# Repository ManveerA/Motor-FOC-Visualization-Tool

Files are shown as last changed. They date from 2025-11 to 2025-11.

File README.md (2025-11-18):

Repository for the project: Real-Time Hands-on Tool for Teaching Three-Phase Motor Control

Youtube Demo: https://youtu.be/jReT5BAICFI?si=BRLmQ3dqiokIST9U

Contributors:

Manveer Aujla - manveeraujla0226@gmail.com

Gavin Feher - gavin.feher@gmail.com

Adam DePinto - depintoadam@gmail.com

Last updated: 2025-11-17

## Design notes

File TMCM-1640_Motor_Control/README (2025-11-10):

The Trinamic Motion Control Language (TMCL) script for controlling the TMCM-1640 controller/driver to drive the QBL4208 BLDC motor.
Author: Manveer Aujla
Contact: manveeraujla0226@gmail.com

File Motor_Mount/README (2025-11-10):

Design files for the custom 3D-printed coupled motor mount.
Designer: Adam DePinto
Contact: depintoadam@gmail.com

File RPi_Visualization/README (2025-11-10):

All files pertaining to the visualization, including the Python script running on the Raspberry Pi and the TI LAUNCHXL-F28379D (LaunchPad) MCU firmware code.
Author: Gavin Feher
Contact: gavin.feher@gmail.com

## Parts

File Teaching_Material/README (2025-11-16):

FOC teaching materials for the proposed approach.

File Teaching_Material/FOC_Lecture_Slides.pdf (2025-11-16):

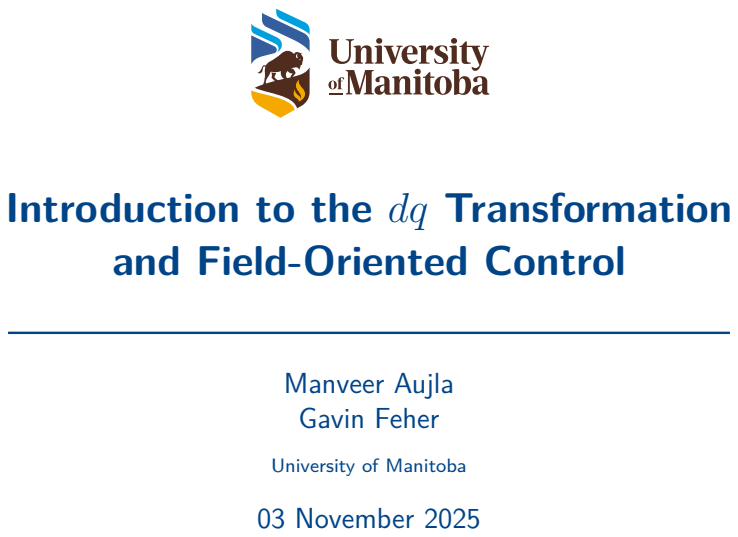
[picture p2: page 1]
Manveer Aujla Gavin Feher; 03 November 2025

Introduction to the dq Transformation
and Field-Oriented Control

University of Manitoba

## The Control Problem

In general,
- Speed control requires torque control for actuation
- Torque control is also current control from proportionality: τ = Kτ i
- Bandwidth: Torque ≫ Speed

Cascaded Control Structure:

Σ

+
PI | Σ

+
PI | Power Stage | Motor

i

∗ | ei | v | i
Speed Loop | Torque Loop

ω

∗
m | eω | ωm
− | −

## Torque Control in a DC Motor

In four steps,
1. Measure the controlled current flowing into the motor.
2. Compare measured current with the desired current, generating error.
3. Amplify the error signal using a PI to generate a correction signal.
4. Modulate the correction voltage and apply to the motor terminals.

## Three-Phase Motors

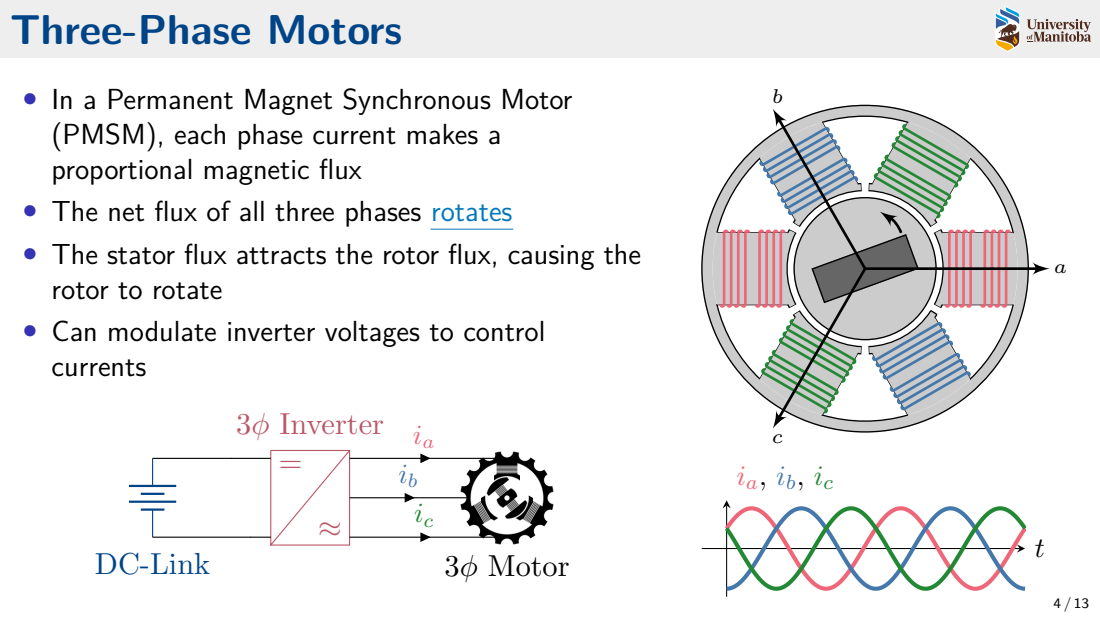
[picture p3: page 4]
DC-Link; 3ϕ Inverter; 3ϕ Motor

• In a Permanent Magnet Synchronous Motor
(PMSM), each phase current makes a
proportional magnetic flux
• The net flux of all three phases rotates (https://www.desmos.com/calculator/sqiyzcerde)
• The stator flux attracts the rotor flux, causing the
rotor to rotate
• Can modulate inverter voltages to control
currents

## The Clarke Transformation

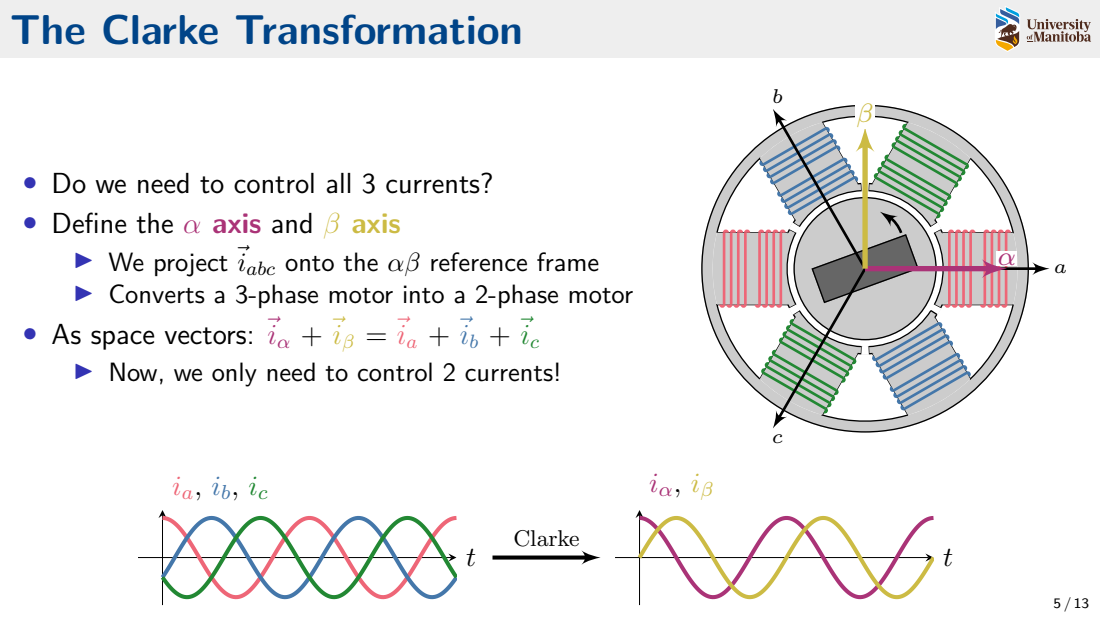
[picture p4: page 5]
Clarke

• Do we need to control all 3 currents?
• Define the α axis and β axis
▶ We project ⃗iabc onto the αβ reference frame
▶ Converts a 3-phase motor into a 2-phase motor
• As space vectors: ⃗iα + ⃗iβ = ⃗ia + ⃗ib + ⃗ic
▶ Now, we only need to control 2 currents!

## The Park Transformation

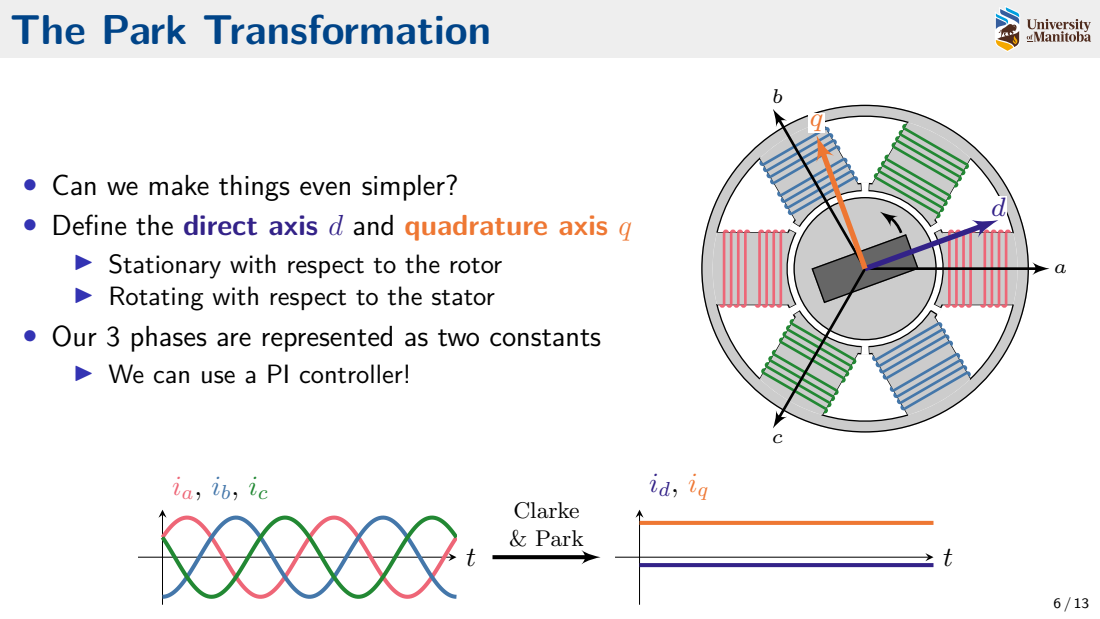
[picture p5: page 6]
Clarke & Park

• Can we make things even simpler?
• Define the direct axis d and quadrature axis q
▶ Stationary with respect to the rotor
▶ Rotating with respect to the stator
• Our 3 phases are represented as two constants
▶ We can use a PI controller!

## Modelling the Motor in dq

What relationships describe the motor?
1. Terminal voltage is applied
2. The system has an RL response, except. . .
3. There is cross-coupling , where id affects iq and vice versa. Cross-coupling is also proportional to the speed ωm
4. There is back electromotive force (EMF) proportional to the speed ωm
vd
vq

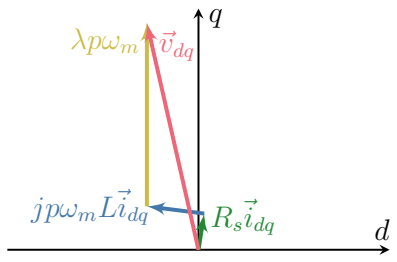
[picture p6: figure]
⃗idq; jpωmL⃗idq; λpωm; ⃗vdq

| {z }
⃗vdq

= Rs

id
iq
| {z }
⃗idq

+L

d

dt
id
iq
+ jpωmL
id
iq
+
0
λpωm

## Maximum Torque Per Amp (MTPA)

θθ

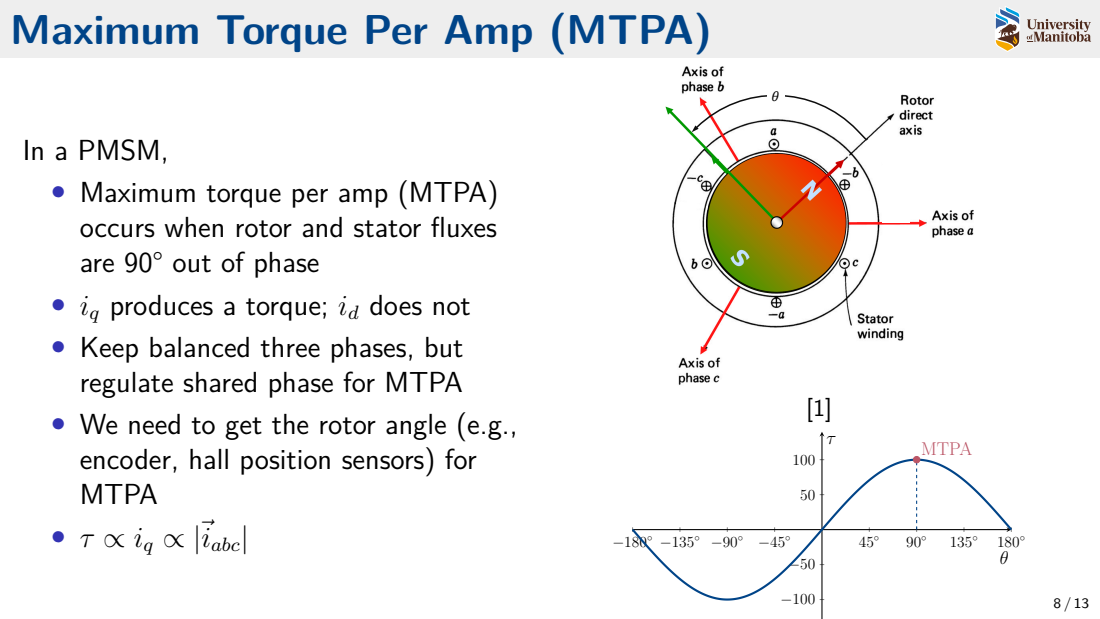
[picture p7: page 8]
• τ ∝ iq ∝ |⃗iabc|; MTPA

In a PMSM,
• Maximum torque per amp (MTPA)
occurs when rotor and stator fluxes
are 90° out of phase
• iq produces a torque; id does not
• Keep balanced three phases, but
regulate shared phase for MTPA
• We need to get the rotor angle (e.g.,
encoder, hall position sensors) for
MTPA

## Field-Oriented Control

θθ

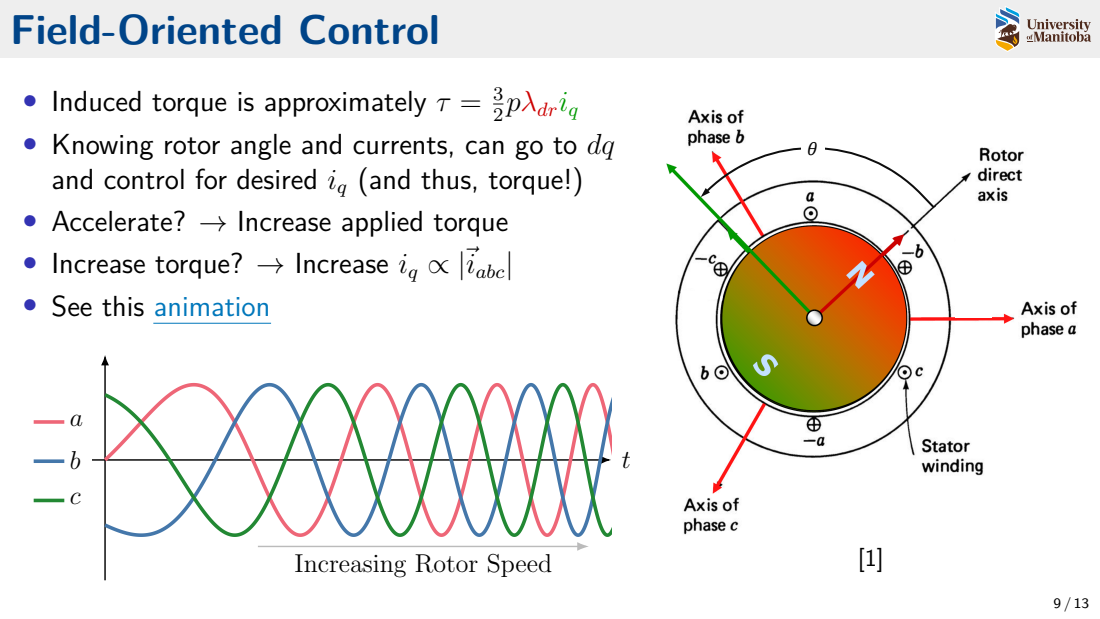
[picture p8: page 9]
3/2 pλdriq

• Induced torque is approximately τ =
• Knowing rotor angle and currents, can go to dq
and control for desired iq (and thus, torque!)
• Accelerate? → Increase applied torque
• Increase torque? → Increase iq ∝ |⃗iabc
• See this animation (https://www.linkedin.com/posts/bingsen-wang-phd-3b062b231_salient-two-pole-synchronous-machine-this-activity-7224932654649856000-Gd2U/)

Increasing Rotor Speed

## Field-Oriented Control Block Diagram Σ

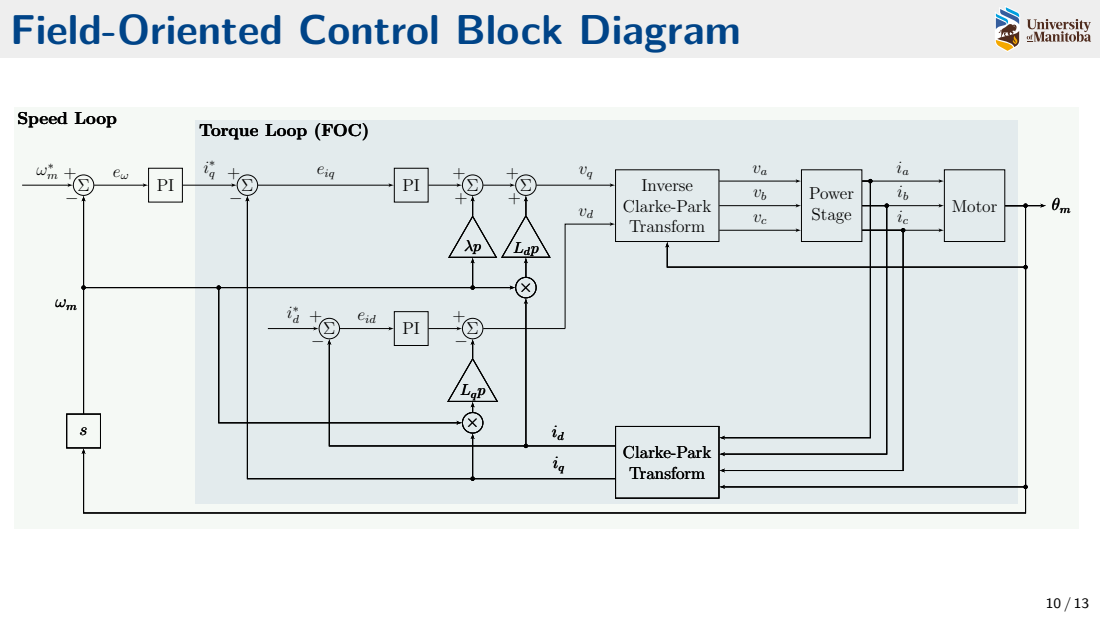
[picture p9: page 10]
eiq; eid; Inverse Clarke-Park Transform; Power Stage; Motor; Clarke-Park Transform; Ldp; Lqp; Speed Loop; Torque Loop (FOC)

## Demo

# Time for a Demo!

## Motor Control Visualization Tool Block Diagram

TMCM Controller & Inverter; HALL; Raspberry Pi; ENC; Voltage & HALL ENC; Current Sensors; TI Launchpad MCU; Sensing & Interfacing PCB; GPIOs; Visualization; HV Energy LV Energy; Information; Mech. Energy; Position Feedback; Δ-Motor; Δ-Generator; Y-Load

## References

[1] D. Wilson, “Intro to Field Oriented Control,” Texas Instruments, 2014. [Online]. Available:
https://eggelectricunicycle.bitbucket.io/EmbeddedFiles/26-02%20Intro%20to%20FOC.pdf (https://eggelectricunicycle.bitbucket.io/EmbeddedFiles/26-02%20Intro%20to%20FOC.pdf)
[2] C. Viana, “Clarke and Park and PMSM Model,” Unpublished, 2025.

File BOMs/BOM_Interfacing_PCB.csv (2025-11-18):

Reference | Value | Footprint | Datasheet | Description | Qty | Part Number
C1,C2,C5,C6,C7,C8,C9,C10,C16,C19,C22,C29,C30 | 0.1u | Capacitor_SMD:C_1206_3216Metric_Pad1.33x1.80mm_HandSolder | https://search.kemet.com/download/datasheet/C1206C104K4RAC7800 | 0.1 µF ±10% 16V Ceramic Capacitor X7R 1206 (3216 Metric) | 13 | C1206C104K4RACTU
C3 | 1u | Capacitor_SMD:C_1206_3216Metric_Pad1.33x1.80mm_HandSolder | https://search.murata.co.jp/Ceramy/image/img/A01X/G101/ENG/GRM319R71A105KA01-01.pdf | 1 µF ±10% 10V Ceramic Capacitor X7R 1206 (3216 Metric) | 1 | GRM319R71A105KA01D
C4 | 1u | Capacitor_SMD:C_1206_3216Metric_Pad1.33x1.80mm_HandSolder | https://search.murata.co.jp/Ceramy/image/img/A01X/G101/ENG/GRM319R71C105KAA3-01.pdf | 1 µF ±10% 16V Ceramic Capacitor X7R 1206 (3216 Metric) | 1 | GRM319R71C105KAA3D
C11,C12,C13 | 0.18u | Capacitor_SMD:C_1206_3216Metric_Pad1.33x1.80mm_HandSolder | https://www.yageo.com/upload/media/product/productsearch/datasheet/mlcc/UPY-GPHC_X7R_6.3V-to-250V_24.pdf | 0.18 µF ±10% 50V Ceramic Capacitor X7R 1206 (3216 Metric) | 3 | CC1206KKX7R9BB184
C14,C17,C20 | 1n | Capacitor_SMD:C_1206_3216Metric_Pad1.33x1.80mm_HandSolder | https://www.yageo.com/en/Chart/Download/pdf/CC1206FRNPO9BN102 | 1000 pF ±1% 50V Ceramic Capacitor C0G, NP0 1206 (3216 Metric) | 3 | CC1206FRNPO9BN102
C15,C18,C21 | 2.2n | Capacitor_SMD:C_1206_3216Metric_Pad1.33x1.80mm_HandSolder | https://search.kemet.com/download/datasheet/C1206C222K4HACAUTO | Unpolarized capacitor | 3 | C1206C222K4HACAUTO
C23,C24,C25 | 4.7n | Capacitor_SMD:C_1206_3216Metric_Pad1.33x1.80mm_HandSolder | https://www.we-online.com/components/products/datasheet/885012208025.pdf | 4700 pF ±10% 16V Ceramic Capacitor X7R 1206 (3216 Metric) | 3 | 8.85012E+11
C26,C27,C28 | 22p | Capacitor_SMD:C_1206_3216Metric_Pad1.33x1.80mm_HandSolder | https://search.kemet.com/download/datasheet/C1206C220F4HAC7800 | 22 pF ±1% 16V Ceramic Capacitor X8R 1206 (3216 Metric) | 3 | C1206C220F4HACTU
D1,D2 | LTST-C150GKT | LED_SMD:LED_1206_3216Metric_Pad1.42x1.75mm_HandSolder | https://optoelectronics.liteon.com/upload/download/DS-22-98-0004/LTST-C150GKT.pdf | Green 569nm LED Indication - Discrete 2.1V | 2 | LTST-C150GKT
J1,J2,J3 | Conn_01x01_Pin | Connector:Banana_Jack_1Pin | https://www.muellerelectric.com/product_files/986/DS-BU-P72930-@.pdf | Banana Jack Connector Standard Banana Threaded, External (Nut) Red | 3 | BU-P72930-2
J4,J7 | 1935174 | 1935174:CONN_1935174_PXC | https://mm.digikey.com/Volume0/opasdata/d220001/medias/docus/1123/1935174.pdf | 3 Position Wire to Board Terminal Block Horizontal with Board 0.197" (5.00mm) Through Hole | 2 | 1935174
J5,J6 | 1984646 | 1984646:CONN_1984646_PXC | https://mm.digikey.com/Volume0/opasdata/d220001/medias/docus/2450/Combicon%20Compact%20Series.pdf | 5 Position Wire to Board Terminal Block Horizontal with Board 0.138" (3.50mm) Through Hole | 2 | 1984646
J8 | 6130XX21821_61304021821 | 61304021821:61304021821 | https://www.we-online.com/components/products/datasheet/61304021821.pdf | 40 Position Receptacle Connector 0.100" (2.54mm) Through Hole Gold | 1 | 61304021821
R1 | 300R | Resistor_SMD:R_1206_3216Metric_Pad1.30x1.75mm_HandSolder | https://www.seielect.com/catalog/sei-rmcf_rmcp.pdf | 300 Ohms ±1% 0.25W, 1/4W Chip Resistor 1206 (3216 Metric) Automotive AEC-Q200 Thick Film | 1 | RMCF1206FT300R
R2 | 120R | Resistor_SMD:R_1206_3216Metric_Pad1.30x1.75mm_HandSolder | https://www.seielect.com/catalog/sei-rmcf_rmcp.pdf | 120 Ohms ±1% 0.25W, 1/4W Chip Resistor 1206 (3216 Metric) Automotive AEC-Q200 Thick Film | 1 | RMCF1206FT120R
R3,R4,R29,R30 | 0 | Resistor_SMD:R_1206_3216Metric_Pad1.30x1.75mm_HandSolder | https://www.seielect.com/catalog/sei-rmcf_rmcp.pdf | Resistor | 4 | RMCF1206ZT0R00
R5,R8,R9,R12,R13,R16 | 1k | Resistor_SMD:R_1206_3216Metric_Pad1.30x1.75mm_HandSolder | https://www.seielect.com/catalog/sei-rncp.pdf | 1 kOhms ±1% 0.5W, 1/2W Chip Resistor 1206 (3216 Metric) Anti-Sulfur Thin Film | 6 | RNCP1206FTD1K00
R6,R7,R10,R11,R14,R15 | 8.06k | Resistor_SMD:R_1206_3216Metric_Pad1.30x1.75mm_HandSolder | https://www.seielect.com/catalog/sei-rncp.pdf | 8.06 kOhms ±1% 0.5W, 1/2W Chip Resistor 1206 (3216 Metric) Anti-Sulfur Thin Film | 6 | RNCP1206FTD8K06
R17,R19,R21,R23,R25,R27 | 10k | Resistor_SMD:R_1206_3216Metric_Pad1.30x1.75mm_HandSolder | https://www.seielect.com/catalog/sei-rncf.pdf | 10 kOhms ±0.5% 0.333W, 1/3W Chip Resistor 1206 (3216 Metric) Automotive AEC-Q200 Thin Film | 6 | RNCF1206DTE10K0
R18,R20,R22,R24,R26,R28 | 20k | Resistor_SMD:R_1206_3216Metric_Pad1.30x1.75mm_HandSolder | https://www.seielect.com/catalog/sei-rncf.pdf | 20 kOhms ±0.1% 0.333W, 1/3W Chip Resistor 1206 (3216 Metric) Automotive AEC-Q200 Thin Film | 6 | RNCF1206BTE20K0
U1,U2,U3 | MCP602 | Package_DIP:DIP-8_W7.62mm | http://ww1.microchip.com/downloads/en/DeviceDoc/21314g.pdf | Dual 2.7V to 6.0V Single Supply CMOS Op Amps, DIP-8/SOIC-8/TSSOP-8 | 3 | MCP602
U4,U5,U6 | MCP6022 | Package_DIP:DIP-8_W7.62mm | http://ww1.microchip.com/downloads/en/devicedoc/20001685e.pdf | Dual Operational Amplifiers, Rail-to-Rail Input/Output, DIP-8/SOIC-8/TSSOP-8 | 3 | MCP6022
U7,U8,U9 | ACS725LLCTR-05AB-T | ACS725:SOIC127P600X175-8N | https://www.allegromicro.com/-/media/files/datasheets/acs725-datasheet.ashx | High-Accuracy, 3.3V Isolated Current Sensor with Stray Field Rejection | 3 | ACS725LLCTR-05AB-T

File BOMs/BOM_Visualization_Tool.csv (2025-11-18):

Part Number | Description | Link | Qty
277-1578-ND | TERM BLK 3POS SIDE ENTRY 5MM PCB | https://www.digikey.ca/en/products/detail/phoenix-contact/1935174/568615?s=N4IgTCBcDa4OxwLQEYCscAciByAREAugL5A | 2
277-1580-ND | TERM BLK 5POS SIDE ENTRY 5MM PCB | https://www.digikey.ca/en/products/detail/phoenix-contact/1935190/568617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 | 1
805.415.65 | Mounting Platform | https://www.ikea.com/ca/en/p/vattenkar-laptop-monitor-stand-birch-80541565/ | 1
B01EV6LJ7G | Breadboard | https://www.amazon.ca/Breadboard-Solderless-Prototype-Distribution-Connecting/dp/B01EV6LJ7G | 1
B01EV70C78 | Jumper Wire Kit | https://www.amazon.ca/Elegoo-120pcs-Multicolored-Breadboard-arduino/dp/B01EV70C78 | 1
B07179VF5J | Banana to Banana Connectors | https://www.amazon.ca/Sumnacon-Stackable-Silicone-Multimeter-Electrical/dp/B07179VF5J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 | 1
B071SL6PQS | Banana to Alligator Connectors | https://www.amazon.ca/Sumnacon-Multimeter-Crocodile-Alligator-Stackable/dp/B071SL6PQS | 1
B07FMV5RMG | Brass Standoff Kit | https://www.amazon.ca/XLX-Male-Female-Female-Female-Assortment-Stainless/dp/B07FMV5RMG | 1
B07FW3GTXB | Cable Sleeve | https://www.amazon.ca/Alex-Tech-10ft-Protector-Sleeving/dp/B07FW3GTXB | 1
B07ZKK6T8S | Rotary Potentiometer | https://www.amazon.ca/Swpeet-Potentiometer-Assortment-Multiturn-HighPrecision/dp/B07ZKK6T8S | 1
B0BM4F65SL | 3D Printer PLA Filament | https://www.amazon.ca/ELEGOO-Filament-Dimensional-Accuracy-Compatible/dp/B0BM4F65SL | 1
B0BNNN9RL2 | NEMA 17 Motor Bracket | https://www.amazon.ca/ChgImposs-Bracket-Universal-Multifunction-Mounting/dp/B0BNNN9RL2 | 1
EG1903-ND | SWITCH SLIDE SPDT 200MA 30V | https://www.digikey.ca/en/products/detail/e-switch/EG1218/101726 | 2
LAUNCHXL-F28379D | LAUNCHPAD TMS320F2837XD/2837XS | https://www.digikey.ca/en/products/detail/texas-instruments/LAUNCHXL-F28379D/7219341 | 1
QBL4208-61-04-013-1k | Brushless (BLDC) DC Motor Standard 4000 RPM Incremental 24VDC | https://www.digikey.ca/en/products/detail/analog-devices-inc-maxim-integrated/QBL4208-61-04-013-1K/9950761 | 1
QBL4208-61-04-013 | Brushless (BLDC) DC Motor Standard 4000 RPM 52.4W 24VDC | https://www.digikey.ca/en/products/detail/analog-devices-inc-maxim-integrated/QBL4208-61-04-013/4843438 | 1
Raspberry Pi 5/4 GB | Raspberry Pi 5/4 GB | https://www.pishop.ca/product/raspberry-pi-5-4gb/ | 1
Raspberry Pi 5 Power Supply | Raspberry Pi 27W USB-C Power Supply Black US | https://www.pishop.ca/product/raspberry-pi-27w-usb-c-power-supply-black-us/ | 1
TMCM-1640 | Brushless 24VDC Supply 5A 12 ~ 28.5V Load | https://www.digikey.ca/en/products/detail/analog-devices-inc-maxim-integrated/TMCM-1640/4399639 | 1
TMCM-1640-CABLE | CABLE LOOM FOR TMCM-1640 | https://www.digikey.ca/en/products/detail/analog-devices-inc-maxim-integrated/TMCM-1640-CABLE/4399640 | 2

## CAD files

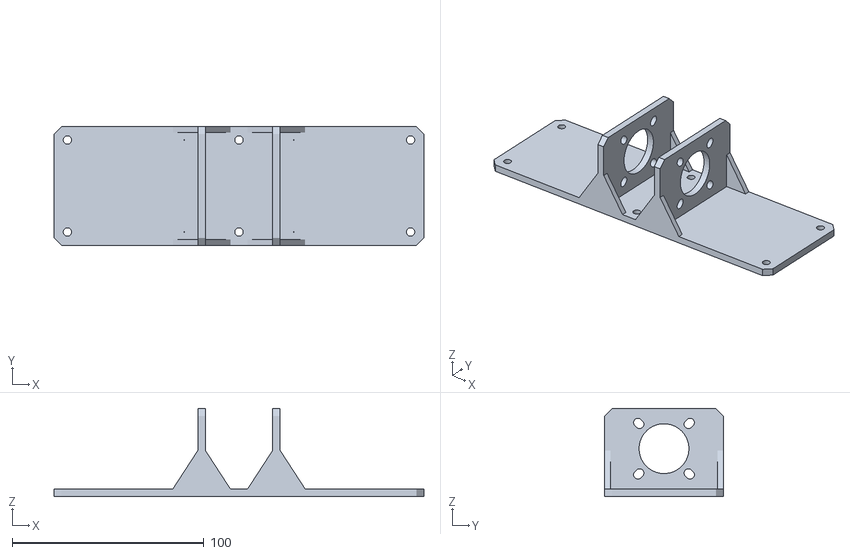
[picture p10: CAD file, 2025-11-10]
Motor_Mount/v2 Capstone BLDC Motor Bracket.stl
193.0 x 62.0 x 46.0

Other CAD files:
Motor_Mount/v2 Capstone BLDC Motor Bracket.f3d

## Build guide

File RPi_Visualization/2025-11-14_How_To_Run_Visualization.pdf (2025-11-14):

Gavin F., Manveer A., Adam D. | 1

Real-Time Hands-on Tool for Teaching Three-Phase Motor Control

### Guide for Running Visualization Tool

Running the Visualization
1) Configure a virtual environment. This is necessary to access the Python libraries needed to run the program. This step only needs to be done when running the visualization for the first time.
2) source [your env. name]/bin/activate: enter a virtual environment to access the Python libraries needed to run the program. Replace [your env. name] with your environment name.
3) cd [path to script]: the path to the script should be the folder where Visualization_1080p.py is located.
4) python Visualization_1080p.py: runs the visualization.

Exporting Data
To export data, simply press the Export button in the bottom right corner. This will save a .csv file of all of the waveforms which are currently displayed in the visualization. It is recommended to pause before exporting to ensure you are saving the correct data. Each row in the .csv will be a different signal. The signals can then be accessed using the following code:

rawData = readmatrix('DataOut.csv');

f = rawData(1,1);

t_analog = rawData(2,:);

uvVolts = rawData(3,:);
vwVolts = rawData(4,:);
wuVolts = rawData(5,:);
dVolts = rawData(6,:);
qVolts = rawData(7,:);
zVolts = rawData(8,:);
uVolts = rawData(9,:);
vVolts = rawData(10,:);
wVolts = rawData(11,:);

uvAmps = rawData(12,:);
vwAmps = rawData(13,:);
wuAmps = rawData(14,:);
dAmps = rawData(15,:);
qAmps = rawData(16,:);
zAmps = rawData(17,:);

speed = rawData(18,:);
refSpeed = rawData(19,:);

dVoltsAvg = rawData(20,:); qVoltsAvg = rawData(21,:);

Gavin F., Manveer A., Adam D.

2
zVoltsAvg = rawData(22,:); dAmpsAvg = rawData(23,:);
qAmpsAvg = rawData(24,:);
zAmpsAvg = rawData(25,:);

t_hall = rawData(26,:);
hallA = rawData(27,:);
hallB = rawData(28,:);
hallC = rawData(29,:);

t_encoder = rawData(30,:); encoderA = rawData(31,:);
encoderB = rawData(32,:);
encoderZ = rawData(33,:);

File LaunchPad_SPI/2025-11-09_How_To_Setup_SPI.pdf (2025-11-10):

Gavin F., Manveer A., Adam D. | 1

Real-Time Hands-on Tool for Teaching Three-Phase Motor Control

### Guide for Setting Up ADC and SPI Between Raspberry Pi 5 and TI LaunchPad

Hardware
Connections between Raspberry Pi 5 (RPi) and LaunchPad (MCU) are as follows.
Notes:
1) Colours in the Signal Name column indicate the colour for the jumper wires used by yours truly.
2) See https://pinout.xyz/ for a Raspberry Pi 5 pinout guide.
3) For ADCA, though ADCINA0 and ADCINA1 exist, they share pins with DACA and DACB, respectively. Thus, for this project, we used ADCINA2 and so on.
4) On the RPi, we chose CE2 for SPI 1 for pinout simplicity.
TI LaunchPad (LAUNCHXL-F28379D) | Raspberry Pi 5
| Signal Name | Datasheet Pin # | Physical Pin # | Signal Name | RPi Pin #
| Ground | J2_10 | GND | Ground | 25
SPI A | MISO / POCI | J2_4 / GPIO59 | 14 | MISO | 21 / GPIO9
| | J2_5 / GPIO58 | 15 | MOSI | 19 / GPIO10 | SPI 0 MOSI / PICO
SCLK | J1_7 / GPIO60 | 7 | SCLK | 23 / GPIO11
| CS / PTE | J2_9 / GPIO61 | 19 | CE0 | 24 / GPIO8
SPI B | MISO / POCI | J6_4 / GPIO64 | 54 | MISO | 35 / GPIO19
| | J6_5 / GPIO63 | 55 | MOSI | 38 / GPIO20 | SPI 1 MOSI / PICO
| SCLK | J5_7 / GPIO65 | 47 | SCLK | 40 / GPIO21
| CS / PTE | J6_9 / GPIO66 | 59 | CE2 | 36 / GPIO16
ADCA | ADCINA2 | J3_9 | 29
| ADCINA3 | J3_6 | 26
| ADCINA4 | J7_9 | 69
ADCB | ADCINB2 | J3_8 | 28
| ADCINB3 | J3_5 | 25
| ADCINB4 | J7_8 | 68

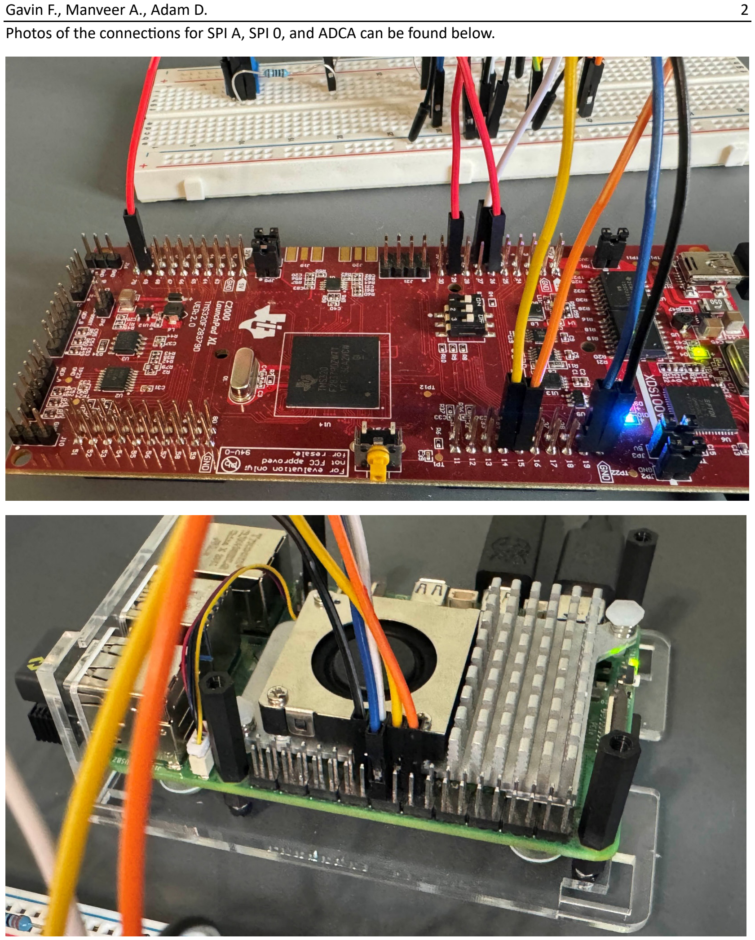
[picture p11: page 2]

Gavin F., Manveer A., Adam D.

2
Photos of the connections for SPI A, SPI 0, and ADCA can be found below.

Gavin F., Manveer A., Adam D. | 3
CCS Programming
For this project, we used Code Composer Studio (CCS) 20.1.1. The steps to make the project are as follows.
1) Open CCS.
2) In the top left corner, choose File then Import Project(s)…
3) Click the Browse… button located next to the Search directory box.
4) Open a similar example to build your program off of. You may find useful examples in
a. C:\ti\C2000Ware_5_04_00_00\driverlib\f2837xd\examples\cpu1
b. C:\ti\C2000Ware_5_04_00_00\training\device\f2837xd
5) Rename project, .c, and .sysconfig files as desired.
6) Change compilation mode from RAM (MCU will not remember the program the next time you plug it in) to FLASH (MCU will yes remember the next time you plug it in). To do this, right click on the project name, go to Build Configurations, and choose the desired method. Note that FLASH will take a significantly longer time to load than RAM.
7) In the .sysconfig file, the EPWM instance controls the sampling frequency. Create a new one, and in EPWM Time Base, the Time Base Period parameter controls the sampling frequency. The Time Base Period for a desired sampling frequency using an up counter can be computed as follows:

# TTPeriod = ffsysclk

# (NNdiv)NNdiv,HSffsample

For example, if we want a sampling frequency of ffsample = 1.25 kHz with a Time Base Clock divider of NNdiv = 4 and a High Speed Clock Divider of NNdiv,HS = 1, we can use the fact that ffsysclk = 50 MHz and

compute as follows:

# TTPeriod = 50 × 106

(4)(1)(1.25 × 103)

= 10000

This means I enter 10000 into the Time Base Period parameter.

To view the sampling frequency, open the EPWM Action Qualifier menu, then ePWMxA Output Configuration, then ePWMxA Event Output Configuration, then change the ePWMxA Time Base counter equals zero parameter to Toggle the output pins. This will toggle the ePWMxA pin every period, meaning if you are measuring with a scope, the sampling frequency will be double the frequency you measure. For example, for EPWM2A, this signal uses J4_8 / GPIO2 which corresponds to physical pin 38.
8) We are now ready to use the ePWM for ADC.

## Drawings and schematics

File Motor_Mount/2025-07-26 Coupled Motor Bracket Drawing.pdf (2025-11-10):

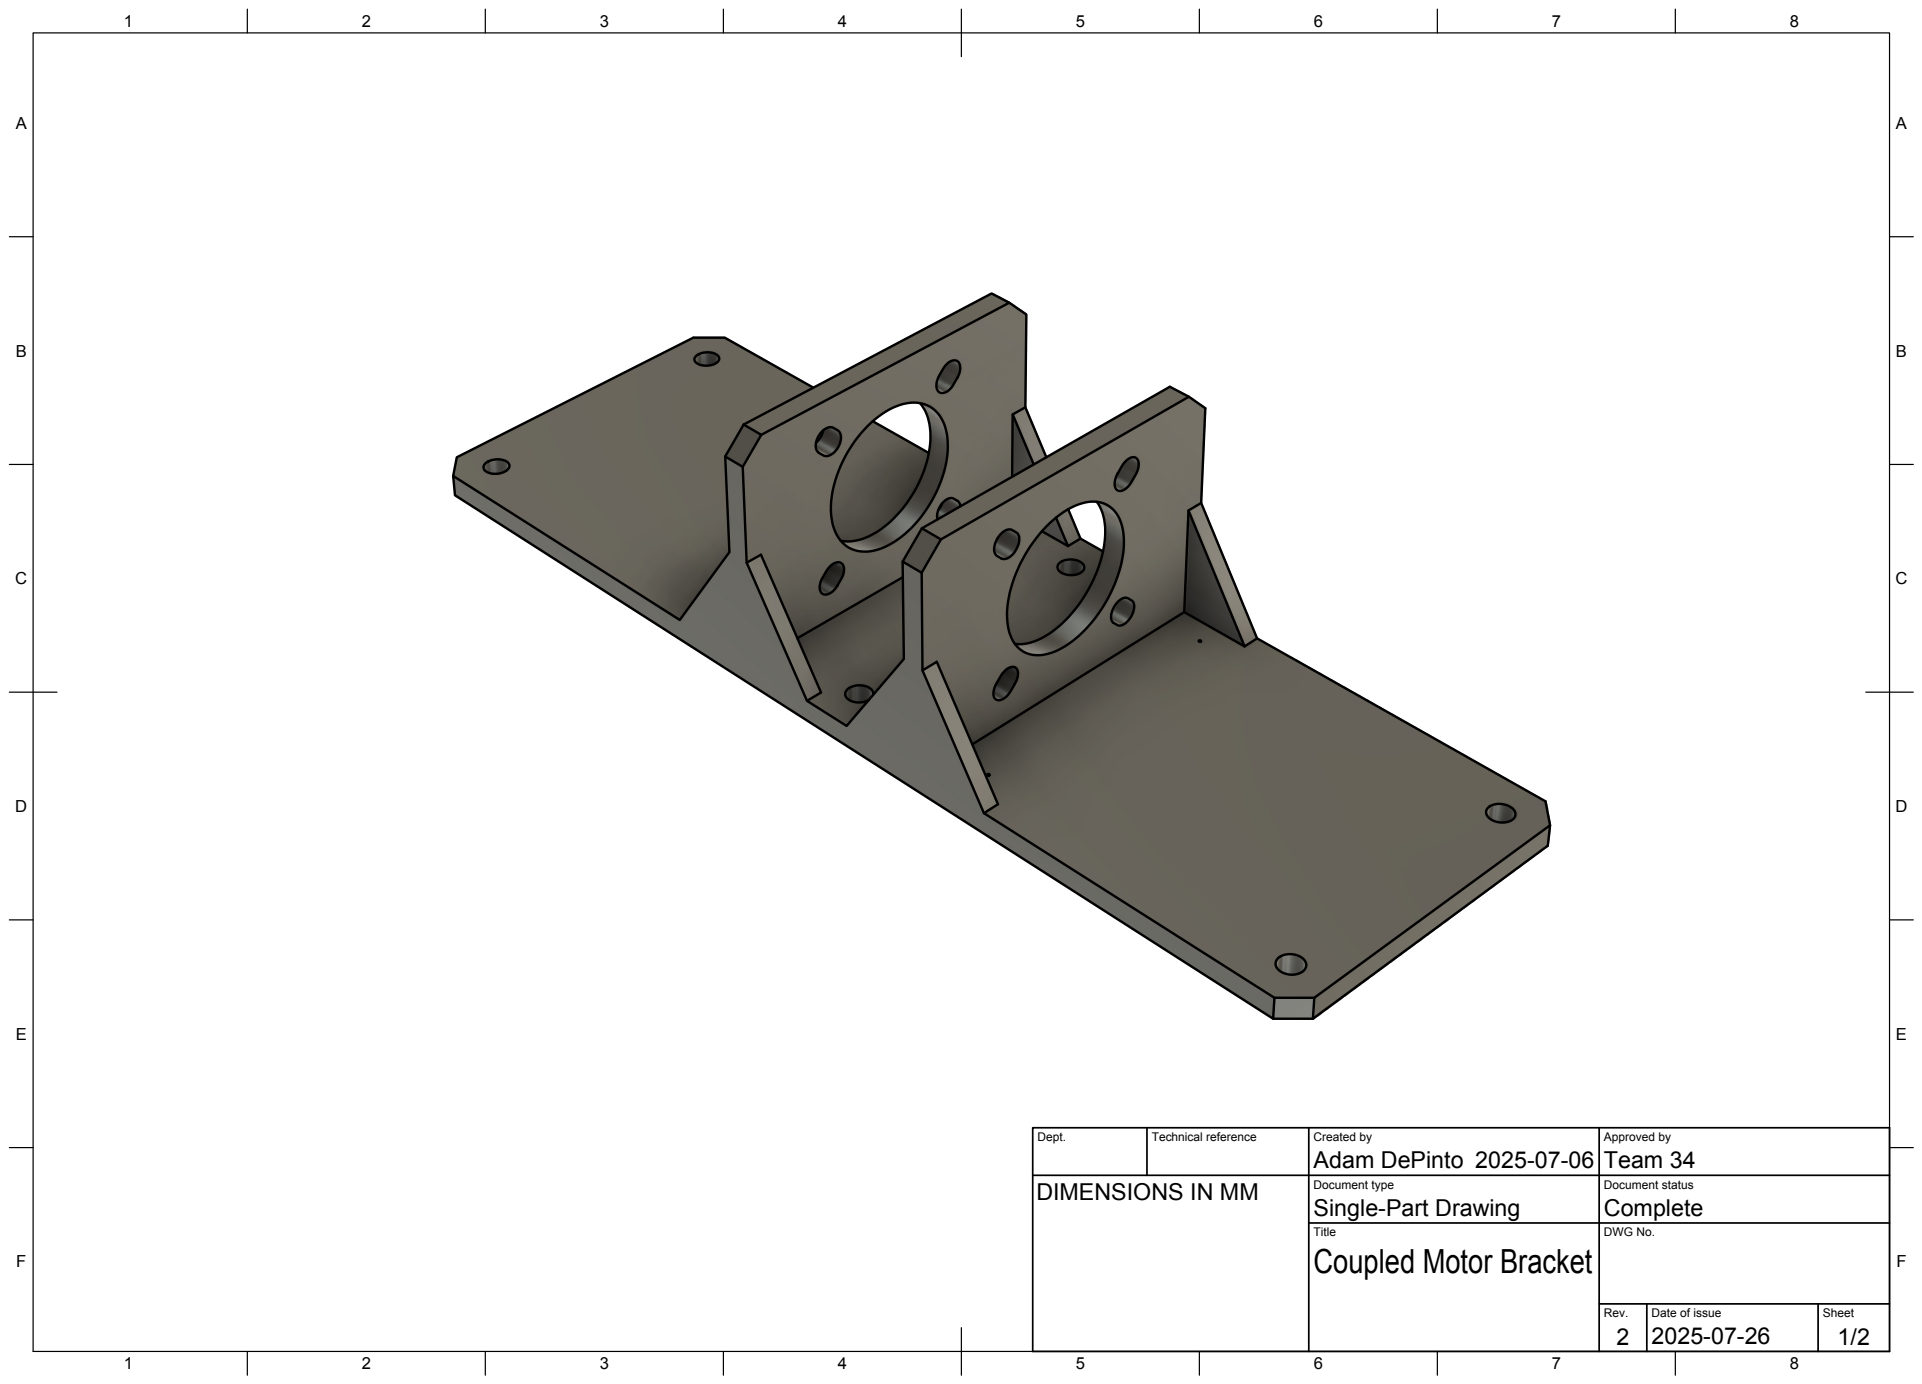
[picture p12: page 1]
Title; DWG No.; Rev.; Date of issue; Sheet

Dept. | Technical reference | Created by Adam DePinto 2025-07-06 | Approved by Team 34

DIMENSIONS IN MM

Document type Single-Part Drawing | Document status Complete

Coupled Motor Bracket

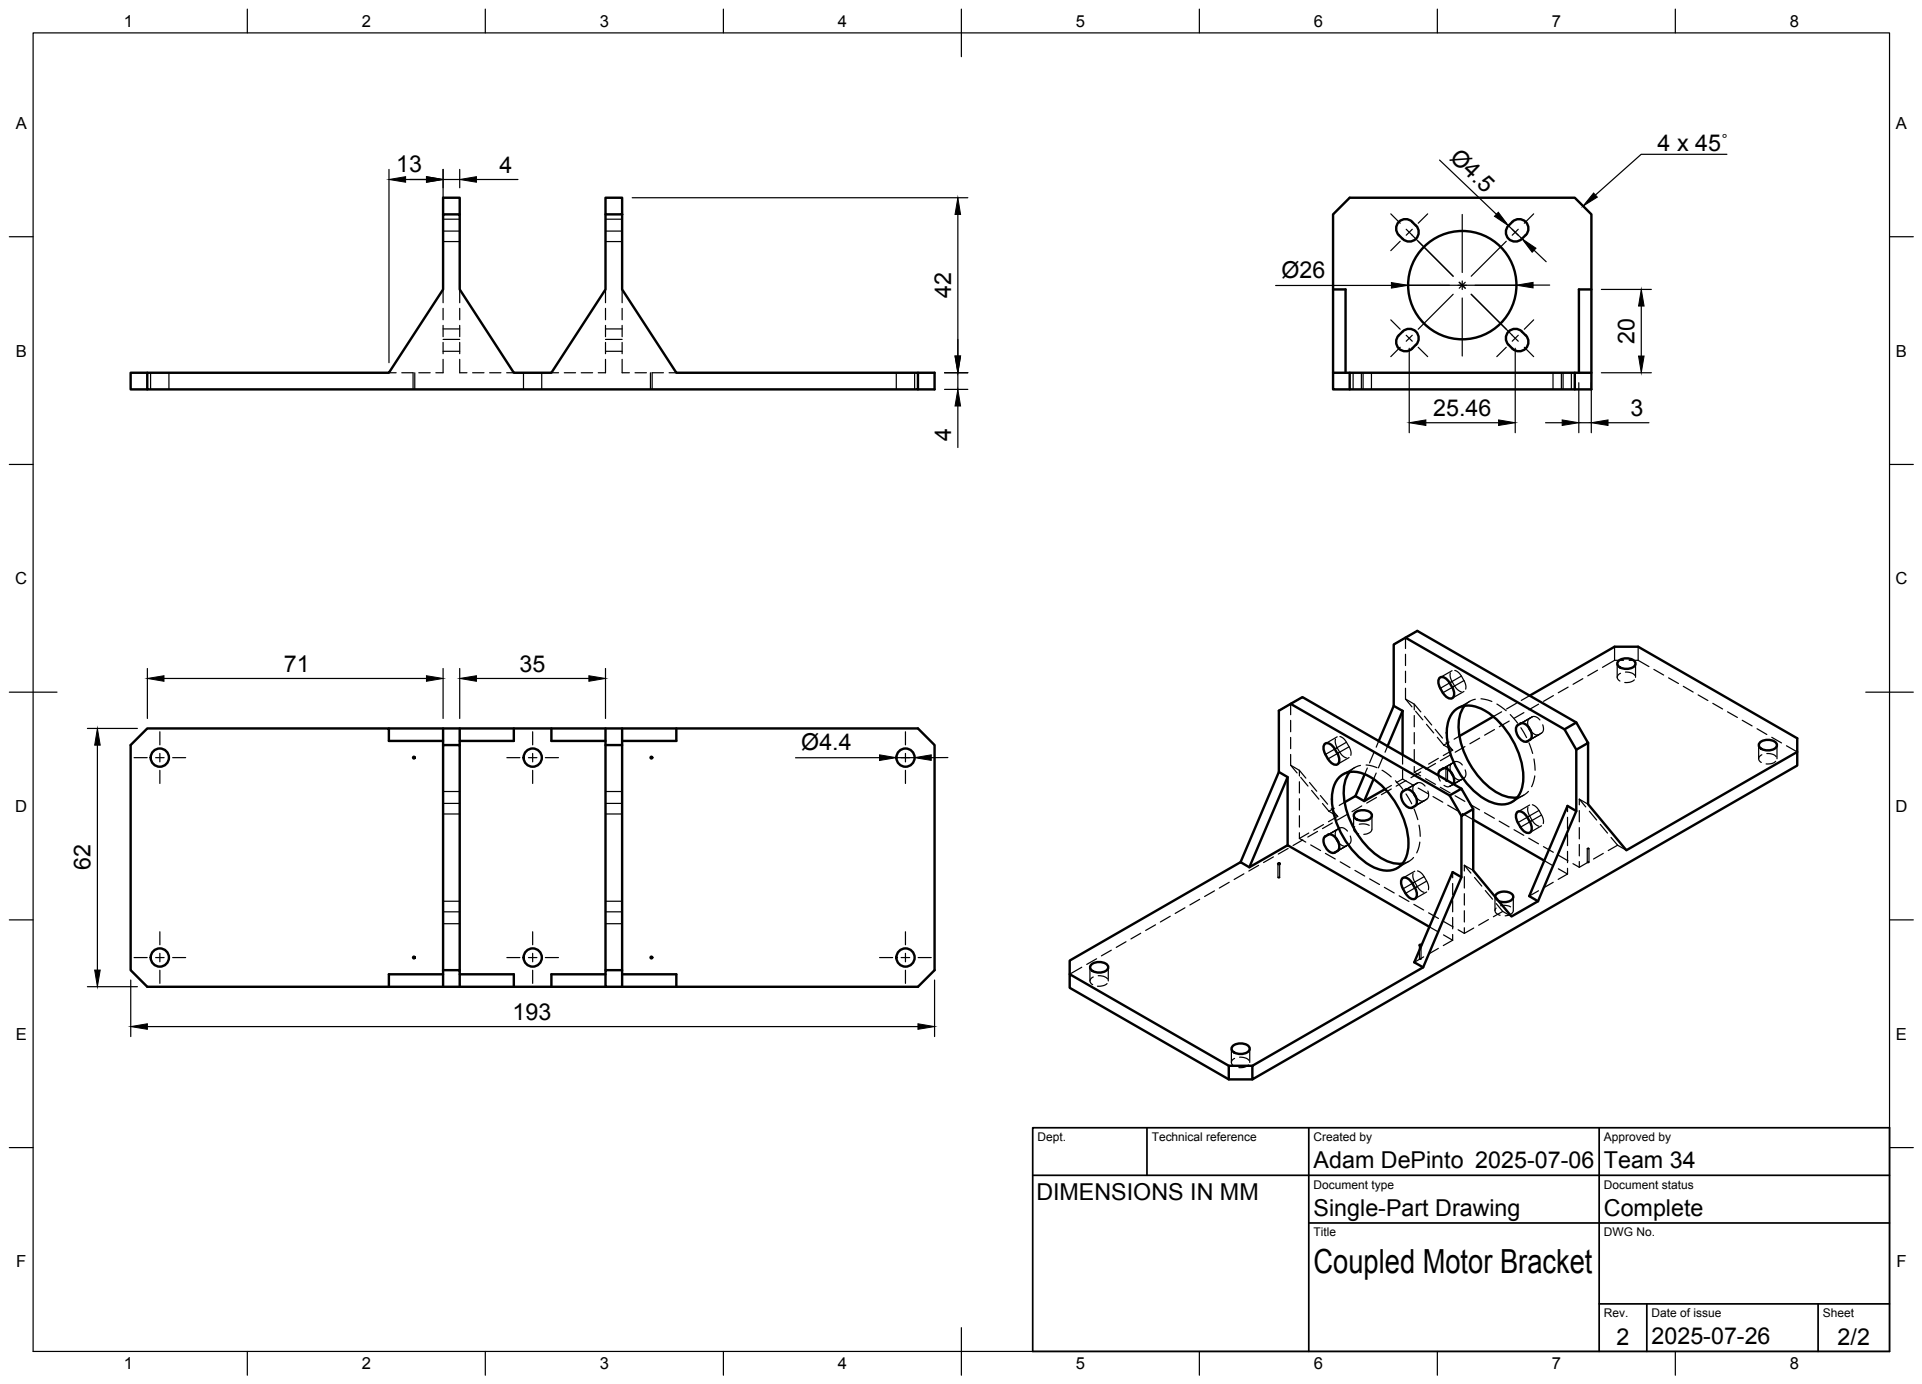
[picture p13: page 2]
Title; DWG No.; Rev.; Date of issue; Sheet

Dept. | Technical reference | Created by Adam DePinto 2025-07-06 | Approved by Team 34

DIMENSIONS IN MM

Document type Single-Part Drawing | Document status Complete

Coupled Motor Bracket

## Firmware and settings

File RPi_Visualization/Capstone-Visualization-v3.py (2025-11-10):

from PyQt5.QtWidgets import QApplication, QMainWindow, QTabWidget, QWidget, QHBoxLayout, QPushButton, QGridLayout, QLabel
from PyQt5.QtGui import QPixmap, QFont
from PyQt5.QtCore import Qt, QSize
from scipy.signal import butter, filtfilt

import pyqtgraph as pg
import sys
import numpy as np
import spidev
import gpiod
import time

class MyWindow(QMainWindow):
    def __init__(self):
        super().__init__()
        self.setWindowTitle("Demonstration of Electromechanical Relationships in a Controlled Electric Motor")
        self.resize(1920, 1080)

        vertLabelFontSize = '30pt'
        legendFontSize = '22pt'

        pg.setConfigOption('foreground', 'k')
        pg.setConfigOption('background', 'w')

        self.tabs = QTabWidget()

        self.tabs.setStyleSheet("""
            QTabBar::tab {
                background: #edeceb;
                color: #000000;
                font-size: 30pt;
                height: 70px;
                width: 290px;
            }
            QTabBar::tab:selected {
                background: #FFFFFF;
                color: #000000;
                outline: none
            }
            QTabBar::tab:focus {
                outline: none
            }
            QTabWidget::pane {
                background: #FFFFFF;
                border: 0;
            }                 
            """)

        self.tabs.currentChanged.connect(self.on_tab_changed)
        self.tabIndex = 0

        # ----- TAB 1 ----- #
        self.timeDomainTab = QWidget()
        grid = QGridLayout()
        
        self.hallLen = 3000
        self.hallPlotLen = 1000
        self.encoderLen = 200
        self.encoderPlotLen = 200
        self.analogLen = 400
        self.analogPlotLen = 200
        self.plotBuffer = 100
        self.speedLen = 101
        self.maxCount = self.hallLen + self.encoderLen + self.analogLen + self.plotBuffer

        self.plotTimeVec = 0.19*np.arange(0,self.analogLen)
        self.hallPlotTimeVec = 0.034*np.arange(0,self.hallPlotLen)
        self.encoderPlotTimeVec = 0.0276*np.arange(0,self.encoderPlotLen)

        vertFont = QFont('Noto Sans', 22)
        vertFont.setWeight(QFont.Light)
        horizFont = QFont('Noto Sans', 22)
        horizFont.setWeight(QFont.Light)
        speedFont = QFont('Noto Sans', 15)
        speedFont.setWeight(QFont.Light)

        plotLineWidth = 6

        # UVW Motor Phase Voltages
        voltagePlot = pg.PlotWidget()
        voltagePlot.setLabel('left','Voltage (V)', **{'font-size': vertLabelFontSize})
        voltagePlot.showGrid(x = True, y = True, alpha = 0.2)
        voltagePlot.setYRange(-23, 23)
        voltagePlot.getPlotItem().getAxis('left').setTicks([[(i, f"{i:.0f}") for i in [x * 10 for x in range(-2, 3)]]])
        voltagePlot.addLegend(offset = (0,0), labelTextSize = legendFontSize, colCount = 3)
        voltagePlot.getAxis('left').setStyle(tickFont = vertFont)
        voltagePlot.getAxis('bottom').setStyle(tickFont = horizFont)
        grid.addWidget(voltagePlot, 0, 0)

        self.uVolts = np.zeros(self.analogLen) # c95564, 81cca2, 8998d9
        self.uVoltsCurve = voltagePlot.plot(self.plotTimeVec[0:self.analogPlotLen],self.uVolts[0:self.analogPlotLen], pen = pg.mkPen(color = '#EE6677', width = plotLineWidth), name = 'UV')

        self.vVolts = np.zeros(self.analogLen)
        self.vVoltsCurve = voltagePlot.plot(self.plotTimeVec[0:self.analogPlotLen],self.vVolts[0:self.analogPlotLen], pen = pg.mkPen(color = '#228833', width = plotLineWidth), name = 'VW')

        self.wVolts = np.zeros(self.analogLen)
        self.wVoltsCurve = voltagePlot.plot(self.plotTimeVec[0:self.analogPlotLen],self.wVolts[0:self.analogPlotLen], pen = pg.mkPen(color = '#4477AA', width = plotLineWidth), name = 'WU')
        
        # UVW Motor Phase Currents
        currentPlot = pg.PlotWidget()
        currentPlot.setLabel('left','Current (A)', **{'font-size': '27pt'})
        currentPlot.showGrid(x = True, y = True, alpha = 0.2)
        currentPlot.setYRange(-1.2, 1.2)
        currentPlot.getPlotItem().getAxis('left').setTicks([[(i, f"{i:.1f}") for i in [x * 0.5 for x in range(-2, 3)]]])
        currentPlot.addLegend(offset = (0,0), labelTextSize = legendFontSize, colCount = 3)
        currentPlot.getAxis('left').setStyle(tickFont = vertFont)
        currentPlot.getAxis('bottom').setStyle(tickFont = horizFont)
        grid.addWidget(currentPlot, 0, 1)

        self.uAmps = np.zeros(self.analogLen)
        self.uAmpsCurve = currentPlot.plot(self.plotTimeVec[0:self.analogPlotLen],self.uAmps[0:self.analogPlotLen], pen = pg.mkPen(color = "#66CCEE", width = plotLineWidth), name = 'UV')

        self.vAmps = np.zeros(self.analogLen)
        self.vAmpsCurve = currentPlot.plot(self.plotTimeVec[0:self.analogPlotLen],self.vAmps[0:self.analogPlotLen], pen = pg.mkPen(color = "#AA3377", width = plotLineWidth), name = 'VW')

        self.wAmps = np.zeros(self.analogLen)
        self.wAmpsCurve = currentPlot.plot(self.plotTimeVec[0:self.analogPlotLen],self.wAmps[0:self.analogPlotLen], pen = pg.mkPen(color = "#CCBB44", width = plotLineWidth), name = 'WU')

        # Speed
        self.speedPlot = pg.PlotWidget()
        axis = self.speedPlot.getPlotItem().getAxis('left')
        axis.setLabel('Speed (rpm)', **{'font-size': vertLabelFontSize})
        axis.setWidth(112)
        self.speedPlot.setLabel('bottom','Sample #', **{'font-size': vertLabelFontSize})
        self.speedPlot.showGrid(x = True, y = True, alpha = 0.2)
        self.speedPlot.setYRange(0, 3535)
        self.speedPlot.setXRange(0, 101)
        self.speedPlot.getPlotItem().getAxis('left').setTicks([[(0,'0'),(500,'500'),(1000,'1000'),(1500,'1500'),(2000,'2000'),(2500,'2500'),(3000,'3000'),(3500,'3500'), \
            (-500,'-500'),(-1000,'-1000'),(-1500,'-1500'),(-2000,'-2000'),(-2500,'-2500'),(-3000,'-3000'),(-3500,'-3500')]])
        self.speedPlot.getAxis('left').setStyle(tickFont = speedFont)
        self.speedPlot.getAxis('bottom').setStyle(tickFont = horizFont)
        self.speedPlot.addLegend(offset = 0, labelTextSize = legendFontSize, colCount = 2)
        grid.addWidget(self.speedPlot, 2, 1)

        self.speed = np.zeros(self.speedLen)
        self.speedCurve = self.speedPlot.plot(self.speed, pen = pg.mkPen(color = '#000000', width = plotLineWidth), name = 'Speed')

        self.refSpeed = np.zeros(self.speedLen)
        self.refSpeedVec = np.zeros(self.speedLen+1)
        self.refSpeedCurve = self.speedPlot.plot(self.refSpeedVec[0:(len(self.refSpeedVec)-1)], pen = pg.mkPen(color = '#66CCEE', width = plotLineWidth-2), name = 'Reference')

        # dq0 Voltages
        vdqPlot = pg.PlotWidget()
        vdqPlot.setLabel('left','Voltage (V)', **{'font-size': vertLabelFontSize})
        vdqPlot.setLabel('bottom','T', **{'color': "#ffffff", 'font-size': vertLabelFontSize})
        vdqPlot.showGrid(x = True, y = True, alpha = 0.2)
        vdqPlot.setYRange(-23, 23)
        vdqPlot.getPlotItem().getAxis('left').setTicks([[(i, f"{i:.0f}") for i in [x * 10 for x in range(-2, 3)]]])
        vdqPlot.addLegend(offset = 0, labelTextSize = legendFontSize, colCount = 3)
        vdqPlot.getAxis('left').setStyle(tickFont = vertFont)
        vdqPlot.getAxis('bottom').setStyle(tickFont = horizFont)
        grid.addWidget(vdqPlot, 1, 0)

        self.dVolts = np.zeros(self.analogLen)
        self.dVoltsVec = np.zeros(self.speedLen)
        self.dVoltsCurve = vdqPlot.plot(self.plotTimeVec[0:self.analogPlotLen],self.dVolts[0:self.analogPlotLen], pen = pg.mkPen(color = "#009988", width = plotLineWidth), name = 'd')

        self.qVolts = np.zeros(self.analogLen)
        self.qVoltsVec = np.zeros(self.speedLen)
        self.qVoltsCurve = vdqPlot.plot(self.plotTimeVec[0:self.analogPlotLen],self.qVolts[0:self.analogPlotLen], pen = pg.mkPen(color = "#E98043", width = plotLineWidth), name = 'q')

        self.zVolts = np.zeros(self.analogLen)
        self.zVoltsVec = np.zeros(self.speedLen)
        self.zVoltsCurve = vdqPlot.plot(self.plotTimeVec[0:self.analogPlotLen],self.zVolts[0:self.analogPlotLen], pen = pg.mkPen(color = '#696969', width = plotLineWidth), name = '0')

        # dq0 Currents
        idqPlot = pg.PlotWidget()
        idqPlot.setLabel('left','Current (A)', **{'font-size': '27pt'})
        idqPlot.setLabel('bottom','Time (ms)', **{'font-size': vertLabelFontSize})
        idqPlot.showGrid(x = True, y = True, alpha = 0.2)
        idqPlot.setYRange(-1.2, 1.2)
        idqPlot.getPlotItem().getAxis('left').setTicks([[(i, f"{i:.1f}") for i in [x * 0.5 for x in range(-2, 3)]]])
        idqPlot.addLegend(offset = 0, labelTextSize = legendFontSize, colCount = 3)
        idqPlot.getAxis('left').setStyle(tickFont = vertFont)
        idqPlot.getAxis('bottom').setStyle(tickFont = horizFont)
        grid.addWidget(idqPlot, 1, 1)

        self.dAmps = np.zeros(self.analogLen)
        self.dAmpsVec = np.zeros(self.speedLen)
        self.dAmpsCurve = idqPlot.plot(self.plotTimeVec[0:self.analogPlotLen],self.dAmps[0:self.analogPlotLen], pen = pg.mkPen(color = "#332288", width = plotLineWidth), name = 'd')

        self.qAmps = np.zeros(self.analogLen)
        self.qAmpsVec = np.zeros(self.speedLen)
        self.qAmpsCurve = idqPlot.plot(self.plotTimeVec[0:self.analogPlotLen],self.qAmps[0:self.analogPlotLen], pen = pg.mkPen(color = "#CC6677", width = plotLineWidth), name = 'q')

        self.zAmps = np.zeros(self.analogLen)
        self.zAmpsVec = np.zeros(self.speedLen)
        self.zAmpsCurve = idqPlot.plot(self.plotTimeVec[0:self.analogPlotLen],self.zAmps[0:self.analogPlotLen], pen = pg.mkPen(color = '#696969', width = plotLineWidth), name = '0')

        # Source Phase Voltages
        motorPhasePlot = pg.PlotWidget()
        axis = motorPhasePlot.getPlotItem().getAxis('left')
        axis.setLabel('Voltage (V)', **{'font-size': vertLabelFontSize})
        axis.setWidth(98)
        motorPhasePlot.setLabel('bottom','Time (ms)', **{'font-size': vertLabelFontSize})
        motorPhasePlot.getPlotItem().getAxis('left').setTicks([[(0,'0'),(5,'5'),(10,'10'),(15,'15'),(20,'20')]])
        motorPhasePlot.showGrid(x = True, y = True, alpha = 0.2)
        motorPhasePlot.setYRange(-1, 21)
        motorPhasePlot.addLegend(offset = 0, labelTextSize = legendFontSize, colCount = 3)
        motorPhasePlot.getAxis('left').setStyle(tickFont = vertFont)
        motorPhasePlot.getAxis('bottom').setStyle(tickFont = horizFont)
        grid.addWidget(motorPhasePlot, 2, 0)

        self.uLineVolts = np.zeros(self.analogLen)
        self.uLineVoltsCurve = motorPhasePlot.plot(self.plotTimeVec[0:self.analogPlotLen],self.uLineVolts[0:self.analogPlotLen], pen = pg.mkPen(color = '#c95564', width = plotLineWidth), name = 'U')

        self.vLineVolts = np.zeros(self.analogLen)
        self.vLineVoltsCurve = motorPhasePlot.plot(self.plotTimeVec[0:self.analogPlotLen],self.vLineVolts[0:self.analogPlotLen], pen = pg.mkPen(color = '#81cca2', width = plotLineWidth), name = 'V')

        self.wLineVolts = np.zeros(self.analogLen)
        self.wLineVoltsCurve = motorPhasePlot.plot(self.plotTimeVec[0:self.analogPlotLen],self.wLineVolts[0:self.analogPlotLen], pen = pg.mkPen(color = '#8998d9', width = plotLineWidth), name = 'W')

        self.plots = [voltagePlot, currentPlot, self.speedPlot, vdqPlot, idqPlot, motorPhasePlot]
        self.timeDomainTab.setLayout(grid)

        # ----- TAB 2 ----- #
        self.vectorTab = QWidget()
        grid = QGridLayout()
        leftCol = QGridLayout()
        rightCol = QGridLayout()

        # Vector plot
        dqPlot = pg.PlotWidget()
        dqPlot.getViewBox().setAspectLocked(True, ratio=1)
        dqPlot.setYRange(-15, 15)
        dqPlot.setXRange(-15, 15)
        dqPlot.setLabel('left','q-axis', **{'font-size': vertLabelFontSize})
        dqPlot.setLabel('bottom','d-axis', **{'font-size': vertLabelFontSize})
        container = QWidget()
        hbox = QHBoxLayout(container)
        hbox.setContentsMargins(0,0,0,0)
        hbox.addStretch(1)
        hbox.addWidget(dqPlot, 10)
        hbox.addStretch(1)
        leftCol.addWidget(container, 1, 0)

        yAxis = pg.PlotDataItem([0, 0], [-30, 30], pen = pg.mkPen(color = "#000000", width = 1))
        dqPlot.addItem(yAxis)
        xAxis = pg.PlotDataItem([-30, 30], [0, 0], pen = pg.mkPen(color = "#000000", width = 1))
        dqPlot.addItem(xAxis)
        dqPlot.getAxis('left').setStyle(tickFont = vertFont)
        dqPlot.getAxis('bottom').setStyle(tickFont = vertFont)

        self.bemfdqVector = pg.PlotDataItem([0, 0], [0, 0], pen = pg.mkPen(color = "#66CCEE", width = plotLineWidth))
        dqPlot.addItem(self.bemfdqVector)
        self.bemfdqCurve = dqPlot.plot([0], [0], symbol = 'o', symbolBrush = pg.mkBrush(color = "#66CCEE", width = plotLineWidth), symbolSize = 25, name = 'Back EMF')

        self.idqVector = pg.PlotDataItem([0, 0], [0, 0], pen = pg.mkPen(color = "#AA3377", width = plotLineWidth))
        dqPlot.addItem(self.idqVector)
        self.idqCurve = dqPlot.plot([0], [0], symbol = 'o', symbolBrush = pg.mkBrush(color = "#AA3377", width = plotLineWidth), symbolSize = 25)

        self.vdqVector = pg.PlotDataItem([0, 0], [0, 0], pen = pg.mkPen(color = "#228833", width = plotLineWidth))
        dqPlot.addItem(self.vdqVector)
        self.vdqCurve = dqPlot.plot([0], [0], symbol = 'o', symbolBrush = pg.mkBrush(color = "#228833", width = plotLineWidth), symbolSize = 25)

        self.CCdqVector = pg.PlotDataItem([0, 0], [0, 0], pen = pg.mkPen(color = "#CCBB44", width = plotLineWidth))
        dqPlot.addItem(self.CCdqVector)
        self.CCdqCurve = dqPlot.plot([0], [0], symbol = 'o', symbolBrush = pg.mkBrush(color = "#CCBB44", width = plotLineWidth), symbolSize = 25)

        self.RsidqVector = pg.PlotDataItem([0, 0], [0, 0], pen = pg.mkPen(color = "#4477AA", width = plotLineWidth))
        dqPlot.addItem(self.RsidqVector)
        self.RsidqCurve = dqPlot.plot([0], [0], symbol = 'o', symbolBrush = pg.mkBrush(color = "#4477AA", width = plotLineWidth), symbolSize = 25)

        legend = pg.LegendItem()
        legend.setParentItem(dqPlot.getPlotItem())
        fontSize = 30
        legend.addItem(self.vdqCurve, f'<span style="font-size:{fontSize}pt;">v<sub>dq</sub> Measured</span>')
        legend.addItem(self.idqCurve, f'<span style="font-size:{fontSize}pt;">v<sub>dq</sub> Estimated</span>')
        legend.addItem(self.RsidqCurve, f'<span style="font-size:{fontSize}pt;">R<sub>s</sub> \U000000d7 i<sub>dq</sub></span>')
        legend.addItem(self.CCdqCurve, f'<span style="font-size:{fontSize}pt;">Cross Coupling</span>')
        legend.addItem(self.bemfdqCurve, f'<span style="font-size:{fontSize}pt;">Back EMF</span>')
        legend.anchor((0, 0), (0, 0))
        legend.setOffset((130, -100))

        equationLabel = QLabel(
            '<span style="color:#AA3377; font-size:30pt; font-weight: bold;">dq Voltage </span>'
            '<span style="color:#000000; font-size:30pt;">&asymp;</span>'
            '<span style="color:#4477AA; font-size:30pt; font-weight: bold;"> Stator Reaction</span>'
            '<span style="color:#000000; font-size:30pt;"> +</span>'
            '<span style="color:#CCBB44; font-size:30pt; font-weight: bold;"> Cross Coupling</span>'
            '<span style="color:#000000; font-size:30pt;"> +</span>'
            '<span style="color:#66CCEE; font-size:30pt; font-weight: bold;"> Back EMF</span>'
        )

        equationLabel.setContentsMargins(0,0,0,0)
        equationLabel.setStyleSheet('padding-bottom: 5px; padding-left: 80px; padding-right: 0px;')
        leftCol.addWidget(equationLabel, 0, 0, alignment=Qt.AlignCenter)

        dqVoltsTimePlot = pg.PlotWidget()
        dqVoltsTimePlot.setLabel('left','Avg. Voltage (V)', **{'font-size': vertLabelFontSize})
        dqVoltsTimePlot.showGrid(x = True, y = True, alpha = 0.2)
        dqVoltsTimePlot.setYRange(-23, 23)
        dqVoltsTimePlot.setXRange(0, self.speedLen)
        dqVoltsTimePlot.getPlotItem().getAxis('left').setTicks([[(i, f"{i:.0f}") for i in [x * 10 for x in range(-2, 3)]]])
        dqVoltsTimePlot.getAxis('left').setStyle(tickFont = vertFont)
        dqVoltsTimePlot.getAxis('bottom').setStyle(tickFont = horizFont)
        dqVoltsTimePlot.addLegend(offset = 0, labelTextSize = legendFontSize, colCount = 3)
        rightCol.addWidget(dqVoltsTimePlot, 0, 0)

        self.dVoltsTimeCurve = dqVoltsTimePlot.plot(self.dVoltsVec[0:self.speedLen], pen = pg.mkPen(color = "#009988", width = plotLineWidth), name = 'd')

        self.qVoltsTimeCurve = dqVoltsTimePlot.plot(self.qVoltsVec[0:self.speedLen], pen = pg.mkPen(color = "#E98043", width = plotLineWidth), name = 'q')

        self.zVoltsTimeCurve = dqVoltsTimePlot.plot(self.zVoltsVec[0:self.speedLen], pen = pg.mkPen(color = '#696969', width = plotLineWidth), name = '0')

        dqAmpsTimePlot = pg.PlotWidget()
        dqAmpsTimePlot.setLabel('left','Avg. Current (A)', **{'font-size': '27pt'})
        dqAmpsTimePlot.setLabel('bottom','Sample #', **{'font-size': vertLabelFontSize})
        dqAmpsTimePlot.getPlotItem().getAxis('left').setTicks([[(i, f"{i:.1f}") for i in [x * 0.5 for x in range(-2, 3)]]])
        dqAmpsTimePlot.showGrid(x = True, y = True, alpha = 0.2)
        dqAmpsTimePlot.setYRange(-1.2, 1.2)
        dqAmpsTimePlot.setXRange(0, self.speedLen)
        dqAmpsTimePlot.getAxis('left').setStyle(tickFont = vertFont)
        dqAmpsTimePlot.getAxis('bottom').setStyle(tickFont = horizFont)
        dqAmpsTimePlot.addLegend(offset = 0, labelTextSize = legendFontSize, colCount = 3)
        rightCol.addWidget(dqAmpsTimePlot, 1, 0)

        self.dAmpsTimeCurve = dqAmpsTimePlot.plot(self.dAmpsVec[0:self.speedLen], pen = pg.mkPen(color = "#332288", width = plotLineWidth), name = 'd')

        self.qAmpsTimeCurve = dqAmpsTimePlot.plot(self.qAmpsVec[0:self.speedLen], pen = pg.mkPen(color = "#CC6677", width = plotLineWidth), name = 'q')

        self.zAmpsTimeCurve = dqAmpsTimePlot.plot(self.zAmpsVec[0:self.speedLen], pen = pg.mkPen(color = '#696969', width = plotLineWidth), name = '0')

        grid.addLayout(leftCol, 0, 0)
        grid.addLayout(rightCol, 0, 1)
        self.vectorTab.setLayout(grid)

        # ----- TAB 3 ----- #
        self.rawTab = QWidget()
        grid = QGridLayout()

        hallPlot = pg.PlotWidget()
        hallPlot.setYRange(0, 5)
        hallPlot.setLabel('left','State', **{'font-size': vertLabelFontSize})
        hallPlot.setLabel('bottom','Time (ms)', **{'font-size': vertLabelFontSize})
        hallPlot.getAxis('left').setStyle(tickFont = vertFont)
        hallPlot.getAxis('bottom').setStyle(tickFont = horizFont)
        hallPlot.getPlotItem().getAxis('left').setTicks([[(0,'0'),(1,'1'),(1.5,'0'),(2.5,'1'),(3,'0'),(4,'1')]])
        grid.addWidget(hallPlot, 0, 0)
        hallPlot.showGrid(x = True, y = True, alpha = 0.2)
        hallPlot.addLegend(offset = 1, labelTextSize = legendFontSize)

        self.hallA = np.zeros(self.hallLen)
        self.hallCurveA = hallPlot.plot(self.hallPlotTimeVec,self.hallA[0:self.hallPlotLen], pen = pg.mkPen(color = '#EE6677', width = plotLineWidth), name = 'Hall A')
        
        self.hallB = np.zeros(self.hallLen)
        self.hallCurveB = hallPlot.plot(self.hallPlotTimeVec,self.hallB[0:self.hallPlotLen], pen = pg.mkPen(color = '#228833', width = plotLineWidth), name = 'Hall B')

        self.hallC = np.zeros(self.hallLen)
        self.hallCurveC = hallPlot.plot(self.hallPlotTimeVec,self.hallC[0:self.hallPlotLen], pen = pg.mkPen(color = '#4477AA', width = plotLineWidth), name = 'Hall C')

        encoderPlot = pg.PlotWidget()
        encoderPlot.setYRange(0, 5)
        encoderPlot.setLabel('left','State', **{'font-size': vertLabelFontSize})
        encoderPlot.setLabel('bottom','Time (ms)', **{'font-size': vertLabelFontSize})
        encoderPlot.getAxis('left').setStyle(tickFont = vertFont)
        encoderPlot.getAxis('bottom').setStyle(tickFont = horizFont)
        encoderPlot.getPlotItem().getAxis('left').setTicks([[(0,'0'),(1,'1'),(1.5,'0'),(2.5,'1'),(3,'0'),(4,'1')]])
        grid.addWidget(encoderPlot, 0, 1)
        encoderPlot.showGrid(x = True, y = True, alpha = 0.2)
        encoderPlot.addLegend(offset = 1, labelTextSize = legendFontSize)

        self.encoderA = np.zeros(self.encoderLen)
        self.encoderCurveA = encoderPlot.plot(self.encoderPlotTimeVec, self.encoderA[0:self.encoderPlotLen], pen = pg.mkPen(color = '#66CCEE', width = plotLineWidth), name = 'Encoder A')
        
        self.encoderB = np.zeros(self.encoderLen)
        self.encoderCurveB = encoderPlot.plot(self.encoderPlotTimeVec, self.encoderB[0:self.encoderPlotLen], pen = pg.mkPen(color = '#AA3377', width = plotLineWidth), name = 'Encoder B')

        self.encoderZ = np.zeros(self.encoderLen)
        self.encoderCurveZ = encoderPlot.plot(self.encoderPlotTimeVec, self.encoderZ[0:self.encoderPlotLen], pen = pg.mkPen(color = '#CCBB44', width = plotLineWidth), name = 'Encoder Z')

        self.rawTab.setLayout(grid)

        # ----- TAB HOME ----- #
        self.homeTab = QWidget()
        grid = QGridLayout()
        leftCol = QGridLayout()
        rightCol = QGridLayout()

        homedqPlot = pg.PlotWidget()
        homedqPlot.getViewBox().setAspectLocked(True, ratio=1)
        homedqPlot.setYRange(-15, 15)
        homedqPlot.setXRange(-15, 15)
        homedqPlot.setLabel('left','q-axis', **{'font-size': vertLabelFontSize})
        homedqPlot.setLabel('bottom','d-axis', **{'font-size': vertLabelFontSize})
        container = QWidget()
        hbox = QHBoxLayout(container)
        hbox.setContentsMargins(0,0,0,0)
        hbox.addStretch(1)
        hbox.addWidget(homedqPlot, 10)
        hbox.addStretch(1)
        leftCol.addWidget(container, 1, 0)
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

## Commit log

2025-11-10 Update folder names
    [2025-05-29 LaunchPad-Pi Interfacing.xlsx, v2 Capstone BLDC Motor Bracket.f3d, v2 Capstone BLDC Motor Bracket.stl]
2025-11-10 Modernized files
    [2025-05-29 LaunchPad-Pi Interfacing.xlsx, 2025-11-09_LaunchPad-RPi_Connections.xlsx]
2025-11-14 Add README for FOC teaching materials
2025-11-18 Updated BOMs
    [BOM_Interfacing_PCB.csv, BOM_Visualization_Tool.csv, Capstone_Interfacing_PCB.csv]
